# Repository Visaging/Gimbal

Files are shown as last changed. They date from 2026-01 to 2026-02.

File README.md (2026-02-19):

# Over-Engineered Stick (ESP32-S3 Gimbal)
Because apparently holding a phone parallel to the ground requires too much caloric burn for the modern human, I spent some time engineering a robot to do it for me. This is a custom 3-axis gimbal powered by an ESP32-S3, designed to compensate for your lack of wrist stability and general unwillingness to hold a steady shot.

## The "Why Did I Build This" Stack:
- **MCU:** ESP32-S3-WROOM-1-N8R2 _(Because a simple Arduino wasn't overkill enough)_
- **Sensors:** BMI270 6-Axis IMU _(To feel every single one of your hand tremors)_
- **Drivers:** 3x DRV8313 Three-Phase Drivers _(So the phone floats magically while you do nothing)_
- **Motors:** 2805 140KV Gimbal BLDC Motors _(To turn in exactly the opposite direction like she did)_
- **Power:** Custom 3S Li-Ion BMS with CN3303 Charging & TPS563200 Regulation _(Because USB 5V is for the weak)_

## Key Features
- **Active Stabilization:** Uses high-frequency FOC math to micro-manage gravity so you don't have to use "muscles".
- **Native USB-C:** One cable to code it and charge it, because looking for two different cables is just too much work.
- **3 Operation Modes:**
   * Stabilize: Standard horizon leveling and pan following.
   * Teaching Mode: Disables the motors so you can twist the camera to any weird angle by hand. After 5 seconds of holding it there, the gimbal accepts its new reality and locks that position.
   * Selfie/Statue Mode: A dedicated mode that gives you 6 seconds to pose the camera, then freezes it in place indefinitely because apparently holding a selfie angle is considered cardio now.
<hr></hr>
<details>
  <summary><h2>External Wiring Diagrams</h2></summary>
  
### Battery:

<!--
https://mermaid.live/edit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
-->
<hr></hr>

### Handle wiring:

<!--
https://mermaid.live/edit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
-->
<hr></hr>

### BMI270 Breakout Board:

<!--
https://mermaid.live/edit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
-->
<hr></hr>

### Motors:

<!--
https://mermaid.live/edit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
-->

</details>
<hr></hr>
<details>
  <summary><h2>PCB Schematics</h2></summary>


</details>
<hr></hr>
<details>
  <summary><h2>PCB Layout and Render</h2></summary>


</details>
<hr></hr>
<details>
  <summary><h2>Custom Body (3D Model)</h2></summary>

### Handle:


<hr></hr>

### Handle Top:


<hr></hr>

### Handle Enclosure:


<hr></hr>

### PAN Arm :


<hr></hr>

### ROLL Arm:


<hr></hr>

### PITCH Arm:


<hr></hr>

### PITCH Arm Cover:


<hr></hr>

### Tripod Enclosure:


<hr></hr>

### Tripod Hub:


<hr></hr>

### Tripod Legs:


</details>
<hr></hr>

## Financial Damage Report (Bill of Material)
BOM can be found in the  root older as a .csv, and is also viewable here: [Custom Gimble BOM](https://docs.google.com/spreadsheets/d/1aBBvSRlrgi5838ZnFZRnFuO4f2IFtYvHOy1n1r-4Mq0/edit?usp=sharing)
<details>
  <summary>Lion Circuits Order</summary>
  
Final
Final

</details>
<details>
  <summary>JLCPCB Order</summary>
  




</details>
<details>
  <summary>Carts</summary>
  
### Robu
  
Robu
<hr></hr>

### OnlyScrews

OnlyScrews
<hr></hr>

### ElectroPi

ElectroPi
<hr></hr>

### Evalta

Evalta
<hr></hr>

### DNA Tech India


<hr></hr>

### Amazon
Amazon
</details>

## Future Bugs... I Mean Features (Roadmap)
Things I might add if I ever get bored of it working perfectly

- [ ] Bluetooth App: Control the gimbal with a phone _(because looking at two screens is better than one)._
- [ ] Face Tracking: If I can figure out how to run AI on this chip without it catching fire.

## Liability Waiver (License)
**License:** MIT

Feel free to steal this code, modify it, or sell it. However, if your phone falls out and breaks because you set the PID values wrong, I legally never met you.

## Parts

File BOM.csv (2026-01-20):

Item | Description | Quantity | Unit Price ($) | Total Price ($) | URL | Total ($)
PCBA | PCB | 5 PCB, 2 PCBA | 54 | 54 | https://jlcpcb.com/ | 54
ESP32-S3-WROOM-1-N8R2 | MCU | 1 | 4.6 | 4.6 | https://evelta.com/esp32-s3-wroom-1-n8r2-wifi-bluetooth-module-8mb-flash-2mb-psram-pcb-antenna/ | 58.6
BMI270 Breadout Board | IMU | 1 | 3.1 | 3.1 | https://evelta.com/7semi-bmi323-imu-nano-breakout-board-6dof-accelerometer-gyroscope-with-qwiic/ | 61.7
2805 140KV BLDC Motors | Motors | 3 | 10.83 | 32.49 | https://robu.in/product/2805-140kv-gimbal-brushless-motor/ | 94.19
3.7v 2500mah 18650 Li-Ion Battery | Battery | 3 | 0.87 | 2.61 | https://robocraze.com/products/3-7v-2500mah-18650-li-ion-battery?variant=43194107920608 | 96.8
18650 3×1 Cell Spacer | Cell Spacer | 2 | 0.011 | 0.022 | https://robu.in/product/18650-3x1-battery-cell-spacer-holder/ | 96.822
3S 10A Li-ion 18650 BMS | BMS | 1 | 1.48 | 1.48 | https://robu.in/product/3s-6a-li-ion-18650-charger-protection-board-module-10-8v-11-1v-12-6v/ | 98.302
DS-314 10MM Momentary Push Button | Push Buttons | 3 | 0.22 | 0.66 | https://robu.in/product/red-ds-314-10mm-lock-free-momentary-self-reset-small-push-button-switch/ | 98.962
3A 250V Rocker Swtich | Power Botton | 1 | 0.27 | 0.27 | https://robu.in/product/1-month-warranty-1217/ | 99.232
3mm LED Orange | LED | 8 | 0.014 | 0.112 | https://robu.in/product/3mm-dip-led-orange-50-pcs/ | 99.344
30AWG Silicon Wire (Red) | Connecting Wire | 5 | 0.055 | 0.275 | https://robu.in/product/high-quality-ultra-flexible-30awg-silicone-wire-1000-m-red/ | 99.619
30AWG Silicon Wire (Black) | Connecting Wire | 5 | 0.055 | 0.275 | https://robu.in/product/high-quality-ultra-flexible-30awg-silicone-wire-1000-m-black/ | 99.894
30AWG Silicon Wire (Yellow) | Connecting Wire | 5 | 0.055 | 0.275 | https://robu.in/product/high-quality-ultra-flexible-30awg-silicone-wire-yellow/ | 100.169
30AWG Silicon Wire (Green) | Connecting Wire | 5 | 0.055 | 0.275 | https://robu.in/product/high-quality-ultra-flexible-30awg-silicone-wire-green/ | 100.444
Universal Mobile Holder | Mobile Holder | 1 | 1.45 | 1.45 | https://www.amazon.in/gp/product/B07S9KNGVS | 101.894
M2 and M3 Screws | Mounting Screws | 1 | 4.38 | 4.38 | https://www.amazon.in/gp/product/B0FP53QGD2/ | 106.274
3M VHB Tape | Mounting PCB | 1 | 4.29 | 4.29 | https://onlyscrews.in/products/3m-gp-bonding-tape-12mm-x-5meters? | 110.564
M3 x 10mm Screws | Mounting Screws | 4 | 0.015 | 0.06 | https://onlyscrews.in/products/phillips-csk-m3-x-8mm-pack-of-20? | 110.624
M3 x 8mm Inserts | Mounting Inserts | 4 | 0.029 | 0.116 | https://onlyscrews.in/products/m3-x-8mm-brass-threaded-inserts? | 110.74
M3 x 25mm Screws | Mounting Screws | 3 | 0.026 | 0.078 | https://onlyscrews.in/products/m3-x-25mm-phillips-csk-ss-304-screw? | 110.818
M3 Nylock Nuts | Mounting Nuts | 3 | 0.033 | 0.099 | https://onlyscrews.in/products/m3-nyloc-nuts-ss304? | 110.917
1/4" - 20 D-Ring | Tripod/Clamp Mounting screw | 1 | 4.38 | 4.38 | https://www.amazon.in/SHOPEE-Mounting-Adapter-Camcorder-Stainless/dp/B09S3XQ8R9/ | 115.297
Platform | Total Shipping ($) | Running Total ($)
JLCPCB | 3.86 | 119.157
Amazon | 0 | 119.157
Robu | 1.09 | 120.247
Evalta | 0.49 | 120.737
Robocraze | 1.37 | 122.107
Only Screws | 2.37 | 124.477
Printing Legion (3D Printing) | 15 | 139.477

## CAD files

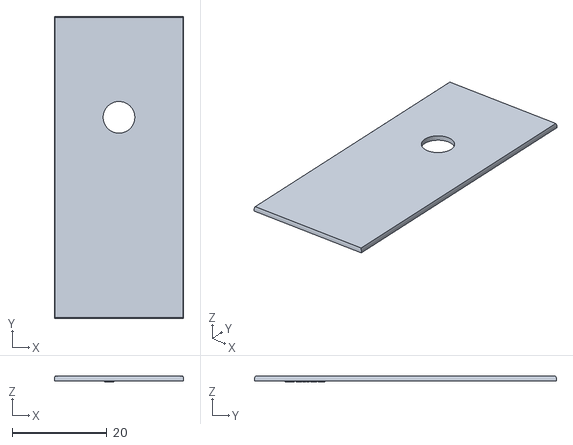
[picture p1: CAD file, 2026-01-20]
CAD/Pitch-Arm-Cover.stl
27.3 x 63.8 x 1.20

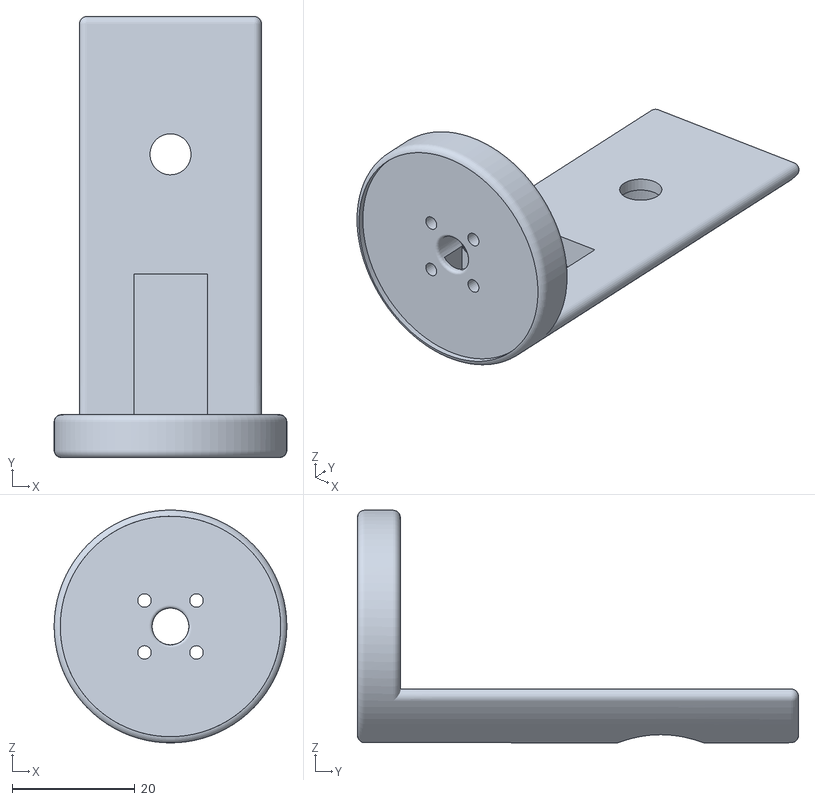
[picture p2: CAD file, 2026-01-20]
CAD/PITCH-Arm.stl
38.0 x 72.0 x 38.0

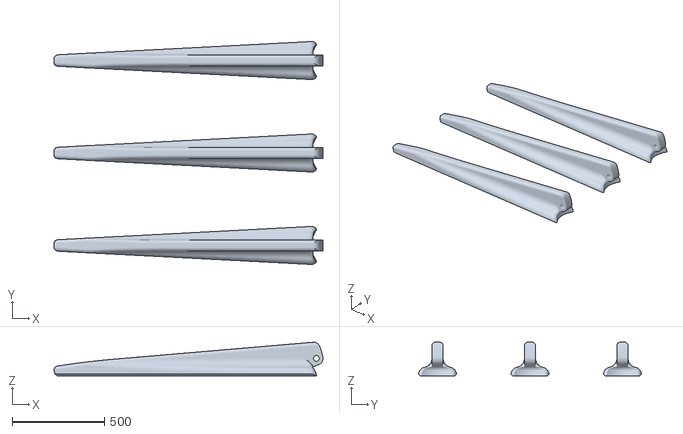
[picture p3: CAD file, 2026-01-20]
CAD/Tripod-Legs.stl
1454.7 x 1205.6 x 181.8

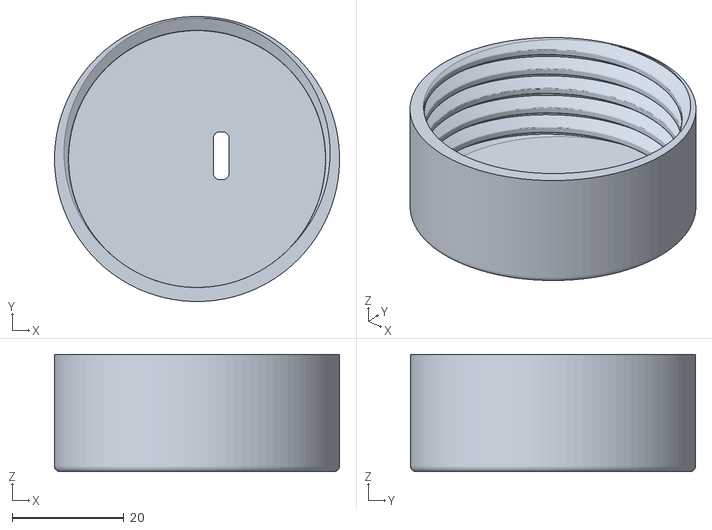
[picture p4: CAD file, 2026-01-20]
CAD/Handle-Enclosure.stl
51.0 x 51.0 x 21.0

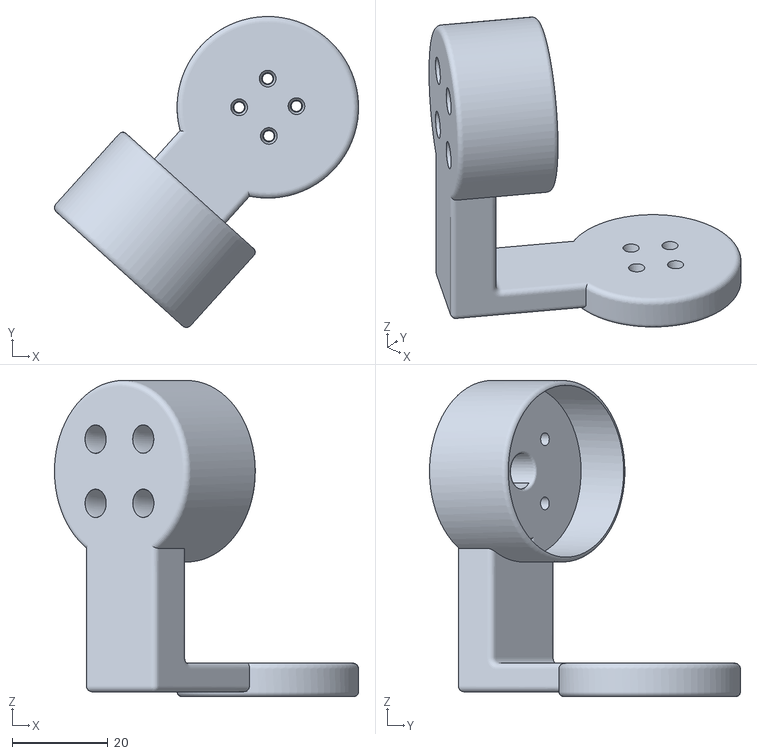
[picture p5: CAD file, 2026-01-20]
CAD/PAN-Arm V2.stl
63.6 x 65.1 x 66.2

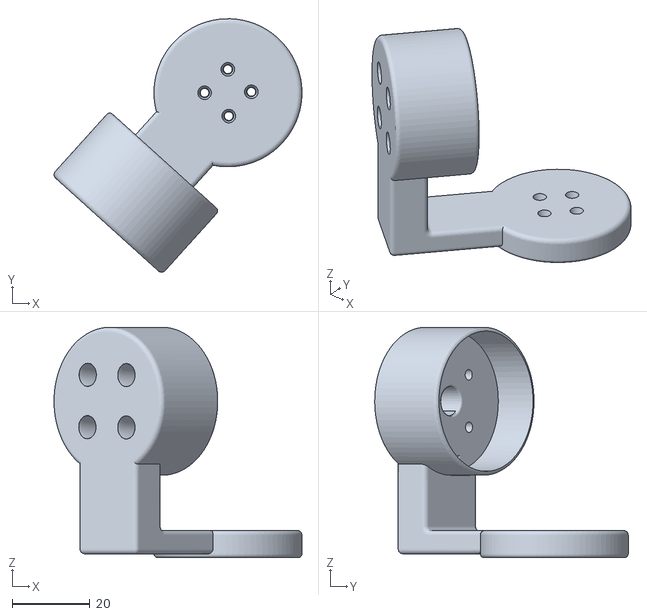
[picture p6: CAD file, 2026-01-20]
CAD/ROLL-Arm V2.stl
63.6 x 65.1 x 59.1

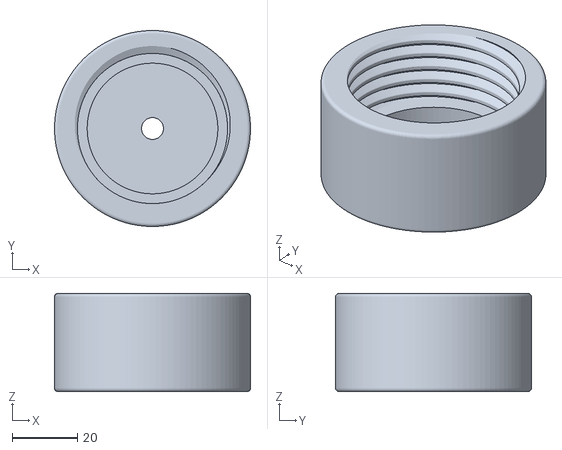
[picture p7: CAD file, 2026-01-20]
CAD/Tripod-Enclosure.stl
60.0 x 60.0 x 30.0

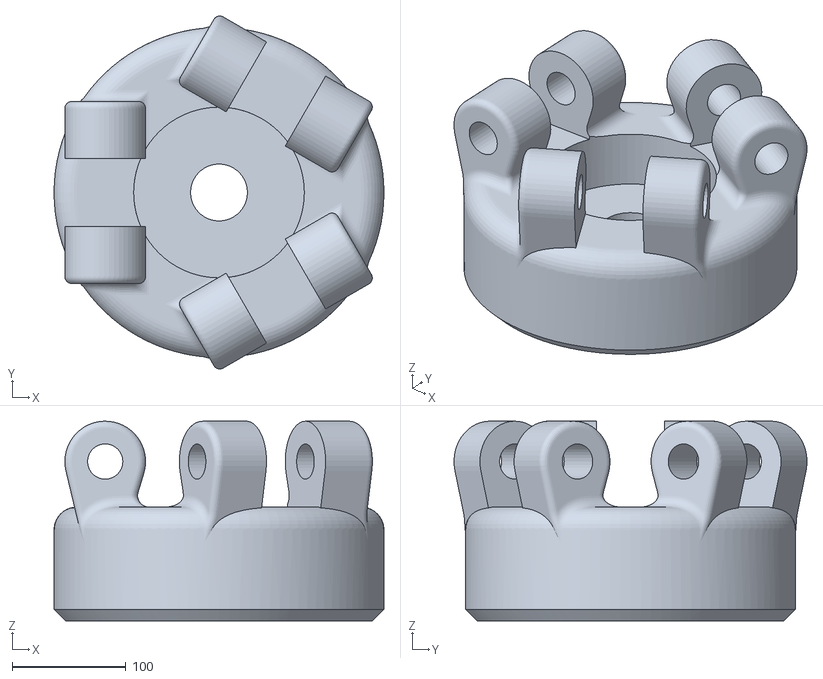
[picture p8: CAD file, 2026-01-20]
CAD/Tripod-Hub.stl
290.0 x 310.3 x 175.5

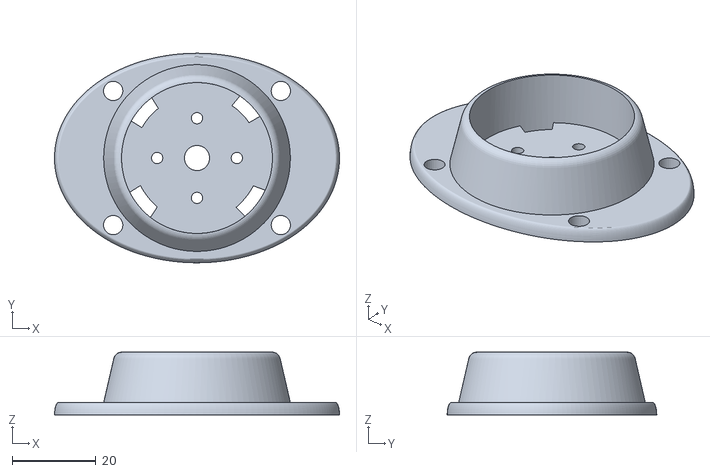
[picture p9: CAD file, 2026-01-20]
CAD/Handle-Top.stl
68.0 x 50.0 x 15.0

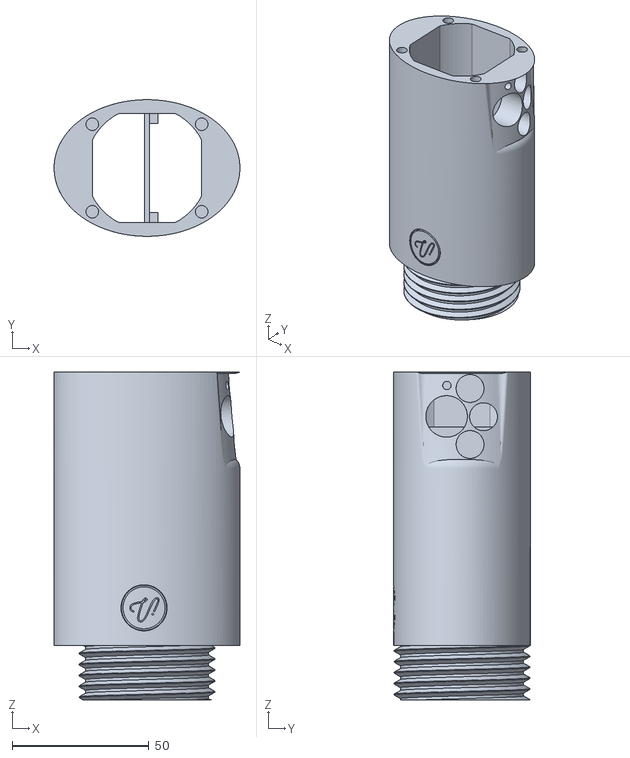
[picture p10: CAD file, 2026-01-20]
CAD/Handle.stl
68.0 x 50.0 x 120.0

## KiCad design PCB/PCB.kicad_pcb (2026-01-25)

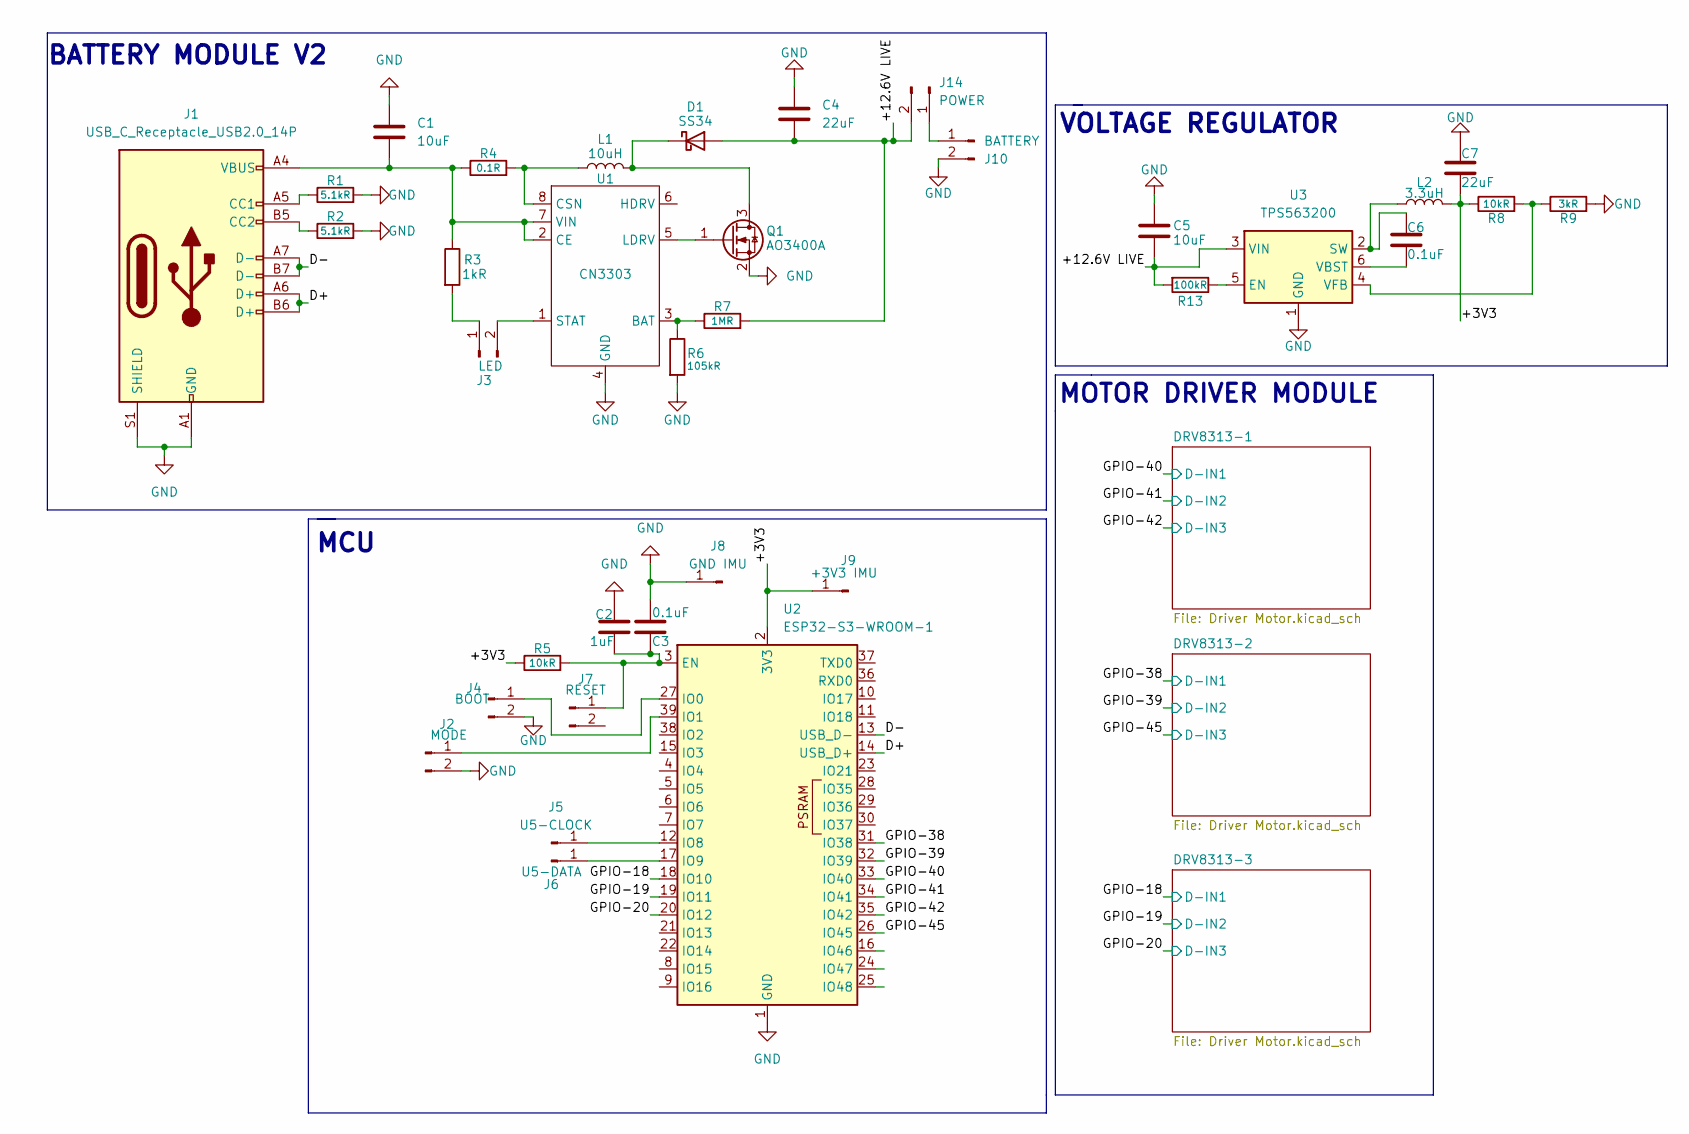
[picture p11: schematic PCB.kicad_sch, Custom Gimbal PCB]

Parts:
C1, C5: 10uF; C_0805_2012Metric
C2: 1uF; C_0805_2012Metric
C3, C6: 0.1uF; C_0805_2012Metric
C4, C7: 22uF; C_0805_2012Metric
D1: SS34; D_SMA
J1: USB_C_Receptacle_USB2.0_14P; USB_C_Receptacle_HRO_TYPE-C-31-M-12
J2: MODE; SolderWire-0.1sqmm_1x02_P3.6mm_D0.4mm_OD1mm
J3: LED; SolderWire-0.1sqmm_1x02_P3.6mm_D0.4mm_OD1mm
J4: BOOT; SolderWire-0.1sqmm_1x02_P3.6mm_D0.4mm_OD1mm
J5: U5-CLOCK; SolderWire-0.1sqmm_1x01_D0.4mm_OD1mm
J6: U5-DATA; SolderWire-0.1sqmm_1x01_D0.4mm_OD1mm
J7: RESET; SolderWire-0.1sqmm_1x02_P3.6mm_D0.4mm_OD1mm
J8: GND IMU; SolderWire-0.1sqmm_1x01_D0.4mm_OD1mm
J9: +3V3 IMU; SolderWire-0.1sqmm_1x01_D0.4mm_OD1mm
J10: BATTERY; SolderWire-0.1sqmm_1x02_P3.6mm_D0.4mm_OD1mm
J14: POWER; SolderWire-0.1sqmm_1x02_P3.6mm_D0.4mm_OD1mm
L1: 10uH; L_Bourns-SRN6028
L2: 3.3uH; L_1210_3225Metric
Q1: AO3400A; SOT-23
R1, R2: 5.1kR; R_0805_2012Metric_Pad1.20x1.40mm_HandSolder
R3: 1kR; R_0805_2012Metric
R4: 0.1R; R_1206_3216Metric
R5, R8: 10kR; R_0805_2012Metric
R6: 105kR; R_0805_2012Metric
R7: 1MR; R_0805_2012Metric
R9: 3kR; R_0805_2012Metric
R13: 100kR; R_0805_2012Metric
U1: CN3303; SOIC-8_3.9x4.9mm_P1.27mm
U2: ESP32-S3-WROOM-1
U3: TPS563200; SOT-23-6

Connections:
/+3V3: C7.1, J9.1, L2.2, R5.1, R8.1, U2.2 (3V3)
/+12.6V LIVE: C4.1, C5.2, D1.2 (A), J14.2, R7.2, R13.2, U3.3 (VIN)
/D+: J1.A6 (D+), J1.B6 (D+), U2.14 (USB_D+)
/D-: J1.A7 (D-), J1.B7 (D-), U2.13 (USB_D-)
/GPIO-18: U2.18 (IO10); also elsewhere on the board
/GPIO-19: U2.19 (IO11); also elsewhere on the board
/GPIO-20: U2.20 (IO12); also elsewhere on the board
/GPIO-38: U2.31 (IO38); also elsewhere on the board
/GPIO-39: U2.32 (IO39); also elsewhere on the board
/GPIO-40: U2.33 (IO40); also elsewhere on the board
/GPIO-41: U2.34 (IO41); also elsewhere on the board
/GPIO-42: U2.35 (IO42); also elsewhere on the board
/GPIO-45: U2.26 (IO45); also elsewhere on the board
GND: C1.1, C2.2, C3.2, C4.2, C5.1, C7.2, J1.A1 (GND), J1.A12 (GND), J1.B1 (GND), J1.B12 (GND), J1.S1 (SHIELD), J2.2, J4.2, J8.1, J10.2, Q1.2 (S), R1.2, R2.2, R6.2, R9.2, U1.4 (GND), U2.1 (GND), U2.40 (GND), U2.41 (GND), U3.1 (GND); also elsewhere on the board
unnamed: D1.1 (K), L1.2, Q1.3 (D)
unnamed: J1.A5 (CC1), R1.1
unnamed: J1.B5 (CC2), R2.1
unnamed: J2.1, U2.39 (IO1)
unnamed: J3.1, R3.2
unnamed: J3.2, U1.1 (STAT)
unnamed: J4.1, U2.27 (IO0)
unnamed: J5.1, U2.12 (IO8)
unnamed: J6.1, U2.17 (IO9)
unnamed: C2.1, C3.1, J7.1, R5.2, U2.3 (EN)
unnamed: J10.1, J14.1
unnamed: Q1.1 (G), U1.5 (LDRV)
unnamed: R6.1, R7.1, U1.3 (BAT)
unnamed: C1.2, J1.A4 (VBUS), J1.A9 (VBUS), J1.B4 (VBUS), J1.B9 (VBUS), R3.1, R4.1, U1.2 (CE), U1.7 (VIN)
unnamed: L1.1, R4.2, U1.8 (CSN)
unnamed: R13.1, U3.5 (EN)
unnamed: C6.1, L2.1, U3.2 (SW)
unnamed: C6.2, U3.6 (VBST)
unnamed: R8.2, R9.1, U3.4 (VFB)

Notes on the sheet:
MOTOR DRIVER MODULE
BATTERY MODULE V2
MCU
VOLTAGE REGULATOR

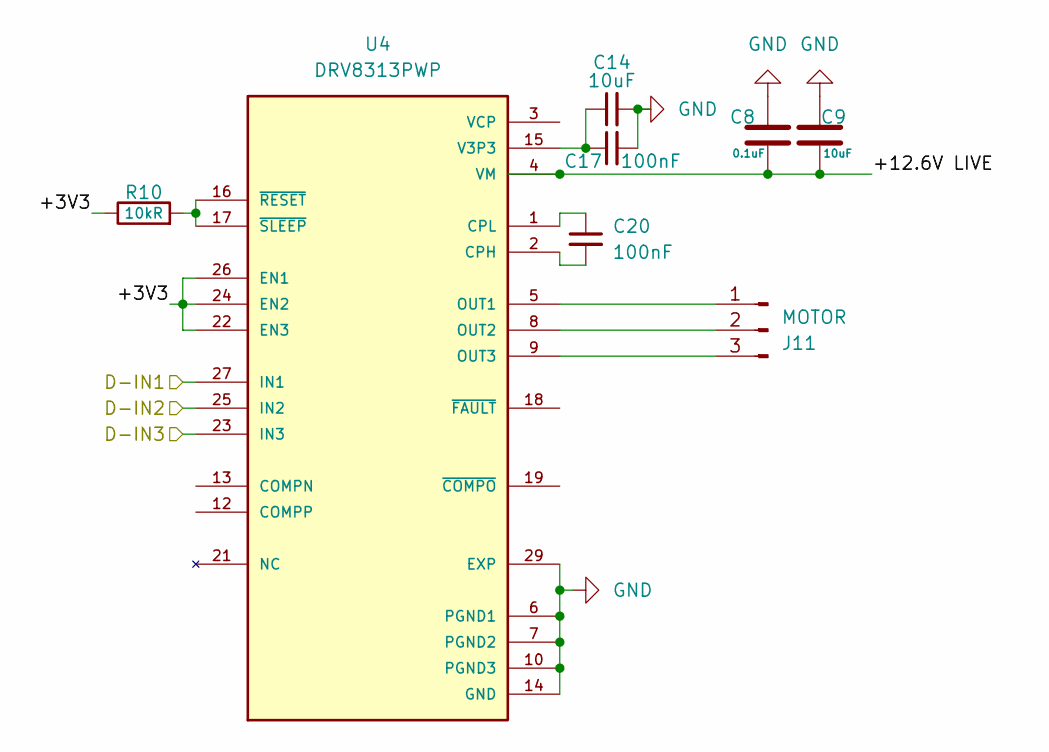
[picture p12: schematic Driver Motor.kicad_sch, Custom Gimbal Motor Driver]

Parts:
C8: 0.1uF; C_0805_2012Metric
C9, C14: 10uF; C_0805_2012Metric
C17, C20: 100nF; C_0805_2012Metric
J11: MOTOR; SolderWire-0.1sqmm_1x03_P3.6mm_D0.4mm_OD1mm
R10: 10kR; R_0805_2012Metric
U4: DRV8313PWP; SOP65P640X120-29N; PARTREV D

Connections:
/DRV8313-1/+3V3: R10.1, U4.22 (EN3), U4.24 (EN2), U4.26 (EN1)
/GPIO-40: U4.27 (IN1); also elsewhere on the board
/GPIO-41: U4.25 (IN2); also elsewhere on the board
/GPIO-42: U4.23 (IN3); also elsewhere on the board
GND: C8.2, C9.1, C14.2, C17.2, U4.6 (PGND1), U4.7 (PGND2), U4.10 (PGND3), U4.14 (GND), U4.20 (GND), U4.28 (GND), U4.29 (EXP); also elsewhere on the board
unnamed: J11.1, U4.5 (OUT1)
unnamed: J11.2, U4.8 (OUT2)
unnamed: J11.3, U4.9 (OUT3)
unnamed: C20.2, U4.2 (CPH)
unnamed: C20.1, U4.1 (CPL)
unnamed: C14.1, C17.1, U4.15 (V3P3)
unnamed: R10.2, U4.16 (~RESET), U4.17 (~SLEEP)
VM: C8.1, C9.2, U4.4 (VM), U4.11 (VM); also elsewhere on the board

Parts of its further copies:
C10, C12: 0.1uF; C_0805_2012Metric
C11, C13, C15, C16: 10uF; C_0805_2012Metric
C18, C19, C21, C22: 100nF; C_0805_2012Metric
J12, J13: MOTOR; SolderWire-0.1sqmm_1x03_P3.6mm_D0.4mm_OD1mm
R11, R12: 10kR; R_0805_2012Metric
U5, U6: DRV8313PWP; SOP65P640X120-29N; PARTREV D

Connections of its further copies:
/DRV8313-2/+3V3: R11.1, U5.22 (EN3), U5.24 (EN2), U5.26 (EN1)
/DRV8313-3/+3V3: R12.1, U6.22 (EN3), U6.24 (EN2), U6.26 (EN1)
/GPIO-18: U6.27 (IN1); also elsewhere on the board
/GPIO-19: U6.25 (IN2); also elsewhere on the board
/GPIO-20: U6.23 (IN3); also elsewhere on the board
/GPIO-38: U5.27 (IN1); also elsewhere on the board
/GPIO-39: U5.25 (IN2); also elsewhere on the board
/GPIO-45: U5.23 (IN3); also elsewhere on the board
GND: C10.2, C11.1, C12.2, C13.1, C15.2, C16.2, C18.2, C19.2, U5.6 (PGND1), U5.7 (PGND2), U5.10 (PGND3), U5.14 (GND), U5.20 (GND), U5.28 (GND), U5.29 (EXP), U6.6 (PGND1), U6.7 (PGND2), U6.10 (PGND3), U6.14 (GND), U6.20 (GND), U6.28 (GND), U6.29 (EXP); also elsewhere on the board
unnamed: J12.1, U5.5 (OUT1)
unnamed: J12.2, U5.8 (OUT2)
unnamed: J12.3, U5.9 (OUT3)
unnamed: J13.1, U6.5 (OUT1)
unnamed: J13.2, U6.8 (OUT2)
unnamed: J13.3, U6.9 (OUT3)
unnamed: C21.2, U5.2 (CPH)
unnamed: C21.1, U5.1 (CPL)
unnamed: C15.1, C18.1, U5.15 (V3P3)
unnamed: R11.2, U5.16 (~RESET), U5.17 (~SLEEP)
unnamed: C22.2, U6.2 (CPH)
unnamed: C22.1, U6.1 (CPL)
unnamed: C16.1, C19.1, U6.15 (V3P3)
unnamed: R12.2, U6.16 (~RESET), U6.17 (~SLEEP)
VM: C10.1, C11.2, C12.1, C13.2, U5.4 (VM), U5.11 (VM), U6.4 (VM), U6.11 (VM); also elsewhere on the board

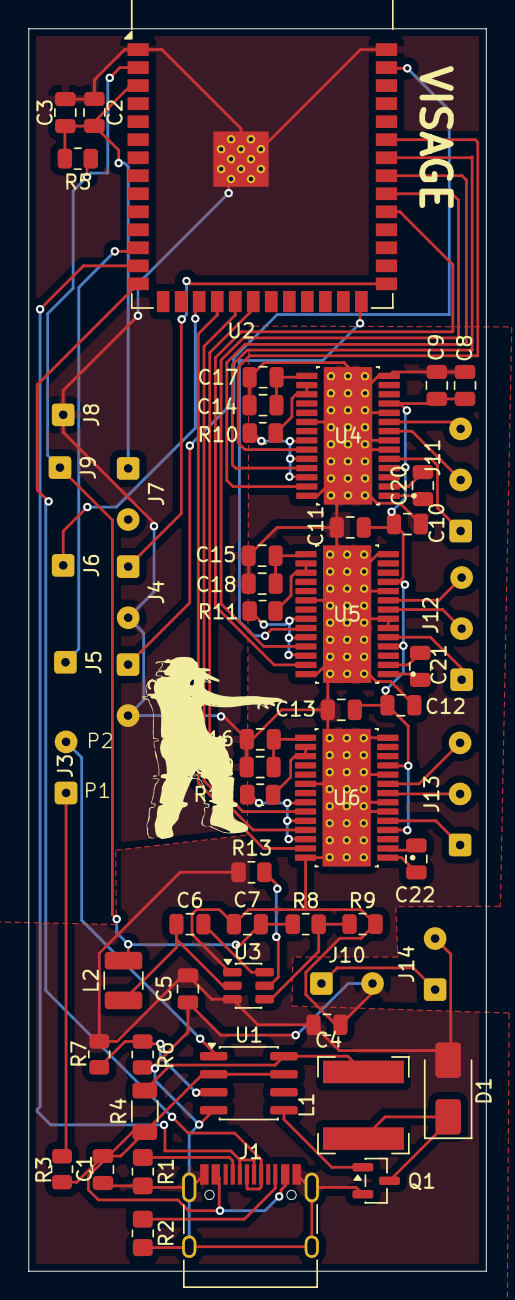
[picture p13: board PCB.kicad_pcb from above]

Board: 2 copper layers, 32.2 x 87.6 mm, 59 parts (0 on the bottom side), 58 nets.

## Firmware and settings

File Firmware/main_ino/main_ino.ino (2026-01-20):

#include <SimpleFOC.h>
#include <SimpleFOCDrivers.h>
#include <Wire.h>
#include "SparkFun_BMI270_Arduino_Library.h"

// PIN DEFINITIONS
#define I2C_SDA_PIN 8  
#define I2C_SCL_PIN 9  

// Motors
#define PITCH_IN1 40
#define PITCH_IN2 41
#define PITCH_IN3 42

#define ROLL_IN1  38
#define ROLL_IN2  39
#define ROLL_IN3  45 

#define YAW_IN1   18
#define YAW_IN2   19
#define YAW_IN3   20

#define MOTOR_EN  14 

// Buttons
#define MODE_BTN_PIN  1
#define BOOT_BTN_PIN  0

// VARIABLES

BMI270 imu; 

BLDCMotor pitch_motor = BLDCMotor(7);
BLDCDriver3PWM pitch_driver = BLDCDriver3PWM(PITCH_IN1, PITCH_IN2, PITCH_IN3, MOTOR_EN);

BLDCMotor roll_motor = BLDCMotor(7);
BLDCDriver3PWM roll_driver = BLDCDriver3PWM(ROLL_IN1, ROLL_IN2, ROLL_IN3, MOTOR_EN);

BLDCMotor yaw_motor = BLDCMotor(7);
BLDCDriver3PWM yaw_driver = BLDCDriver3PWM(YAW_IN1, YAW_IN2, YAW_IN3, MOTOR_EN);

// Targets
float target_pitch = 0;
float target_roll = 0;
float target_yaw = 0;

// Sensor Data
float sensor_pitch = 0;
float sensor_roll = 0;
float estimated_yaw = 0;

// Logic Variables
unsigned long last_time = 0;
int current_mode = 1; 

// State Flags
unsigned long mode_timer_start = 0;
bool mode3_locked = false; 

bool last_mode_btn_state = HIGH; 
bool last_boot_btn_state = HIGH;

// SETUP

void setup() {
  Serial.begin(115200);
  delay(2000);

  Wire.setPins(I2C_SDA_PIN, I2C_SCL_PIN);
  Wire.begin();
  delay(500);

  // --- Drivers ---
  pitch_driver.voltage_power_supply = 12.6;
  pitch_driver.init();
  pitch_motor.linkDriver(&pitch_driver);
  
  roll_driver.voltage_power_supply = 12.6;
  roll_driver.init();
  roll_motor.linkDriver(&roll_driver);
  
  yaw_driver.voltage_power_supply = 12.6;
  yaw_driver.init();
  yaw_motor.linkDriver(&yaw_driver);

  // --- Sensor ---
  if(imu.beginI2C() != BMI2_OK){
    Serial.println("IMU Not Found!");
  }

  // --- Motors ---
  pitch_motor.voltage_limit = 4.0; 
  roll_motor.voltage_limit = 4.0;
  yaw_motor.voltage_limit = 4.0;

  pitch_motor.controller = MotionControlType::angle_openloop;
  roll_motor.controller = MotionControlType::angle_openloop;
  yaw_motor.controller = MotionControlType::angle_openloop;

  pitch_motor.init();
  roll_motor.init();
  yaw_motor.init();

  pinMode(MODE_BTN_PIN, INPUT_PULLUP);
  pinMode(BOOT_BTN_PIN, INPUT_PULLUP);

  Serial.println("Gimbal Ready.");
}


// MAIN LOOP

void loop() {
  // Read Sensor
  imu.getSensorData(); 
  unsigned long now = micros();
  float dt = (now - last_time) * 1e-6; 
  last_time = now;

  // Calculate Angles
  sensor_pitch = atan2(imu.data.accelY, imu.data.accelZ);
  sensor_roll  = -atan2(imu.data.accelX, imu.data.accelZ);

  float gyro_z = imu.data.gyroZ * 0.0174533;
  if (abs(gyro_z) < 0.03) gyro_z = 0;        // Deadband
  estimated_yaw += gyro_z * dt;

  // SMART DRIFT FIX
  if (current_mode == 1 && target_yaw == 0) {
      estimated_yaw *= 0.9995; 
  }

  // Handle Inputs
  handleModeButton(); 
  handleBootButton(); 

  // MODE LOGIC
  if (current_mode == 1) {
    // MODE 1
    pitch_motor.move(target_pitch - sensor_pitch);
    roll_motor.move(target_roll - sensor_roll);
    yaw_motor.move(target_yaw - estimated_yaw);
    
  } 
  else if (current_mode == 2) {
    // MODE 2
    pitch_motor.move(0); roll_motor.move(0); yaw_motor.move(0);

    if (millis() - mode_timer_start > 5000) {
      // Lock targets to current position
      target_pitch = sensor_pitch;
      target_roll = sensor_roll;
      target_yaw = estimated_yaw;
      
      // Restore Power
      pitch_motor.voltage_limit = 4.0;
      roll_motor.voltage_limit = 4.0;
      yaw_motor.voltage_limit = 4.0;
      
      // Go to Mode 1 again
      current_mode = 1; 
      Serial.println("Mode 2 Locked.");
    }
  }
  else if (current_mode == 3) {
    // MODE 3
    
    // Setup Phase
    if (millis() - mode_timer_start < 6000) {
       pitch_motor.move(0); roll_motor.move(0); yaw_motor.move(0);
       mode3_locked = false;
    } 
    // Locked Phase
    else {
       if (!mode3_locked) {
         // Capture targets
         target_pitch = sensor_pitch;
         target_roll = sensor_roll;
         target_yaw = estimated_yaw;
         
         // Restore Power
         pitch_motor.voltage_limit = 4.0;
         roll_motor.voltage_limit = 4.0;
         yaw_motor.voltage_limit = 4.0;
         
         mode3_locked = true;
         Serial.println("Mode 3 Locked.");
       }
       
       // Stabilize
       pitch_motor.move(target_pitch - sensor_pitch);
       roll_motor.move(target_roll - sensor_roll);
       yaw_motor.move(target_yaw - estimated_yaw);
    }
  }

  // FOC Loop
  pitch_motor.loopFOC();
  roll_motor.loopFOC();
  yaw_motor.loopFOC();
}

// FUNCTIONS

void handleModeButton() {
  bool btn = digitalRead(MODE_BTN_PIN);
  if (last_mode_btn_state == HIGH && btn == LOW) {
    delay(50);
    if (digitalRead(MODE_BTN_PIN) == LOW) {

      current_mode = 2;
      mode_timer_start = millis();
      pitch_motor.voltage_limit = 0; 
      roll_motor.voltage_limit = 0;
      yaw_motor.voltage_limit = 0;
      Serial.println("Mode 2: 5s Setup...");
    }
  }
  last_mode_btn_state = btn;
}

void handleBootButton() {
  bool btn = digitalRead(BOOT_BTN_PIN);
  if (last_boot_btn_state == HIGH && btn == LOW) {
    delay(50);
    if (digitalRead(BOOT_BTN_PIN) == LOW) {
      
      if (current_mode != 3) {

        current_mode = 3;
        mode_timer_start = millis();
        mode3_locked = false;
        
        pitch_motor.voltage_limit = 0; 
        roll_motor.voltage_limit = 0;
        yaw_motor.voltage_limit = 0;
        Serial.println("Mode 3: 6s Setup...");
        
      } else {
        // Exit Mode 3 -> Reset to Flat
        current_mode = 1;
        target_pitch = 0;
        target_roll = 0;
        target_yaw = 0;
        estimated_yaw = 0; // Reset Yaw drift
        
        pitch_motor.voltage_limit = 4.0;
        roll_motor.voltage_limit = 4.0;
        yaw_motor.voltage_limit = 4.0;
        Serial.println("Mode 3 Exit: Reset.");
      }
    }
  }
  last_boot_btn_state = btn;
}
